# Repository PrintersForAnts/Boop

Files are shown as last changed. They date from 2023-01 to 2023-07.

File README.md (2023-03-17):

# Boop

Add nozzle probing to your [Printer For Ants](https://www.3dprintersforants.com).

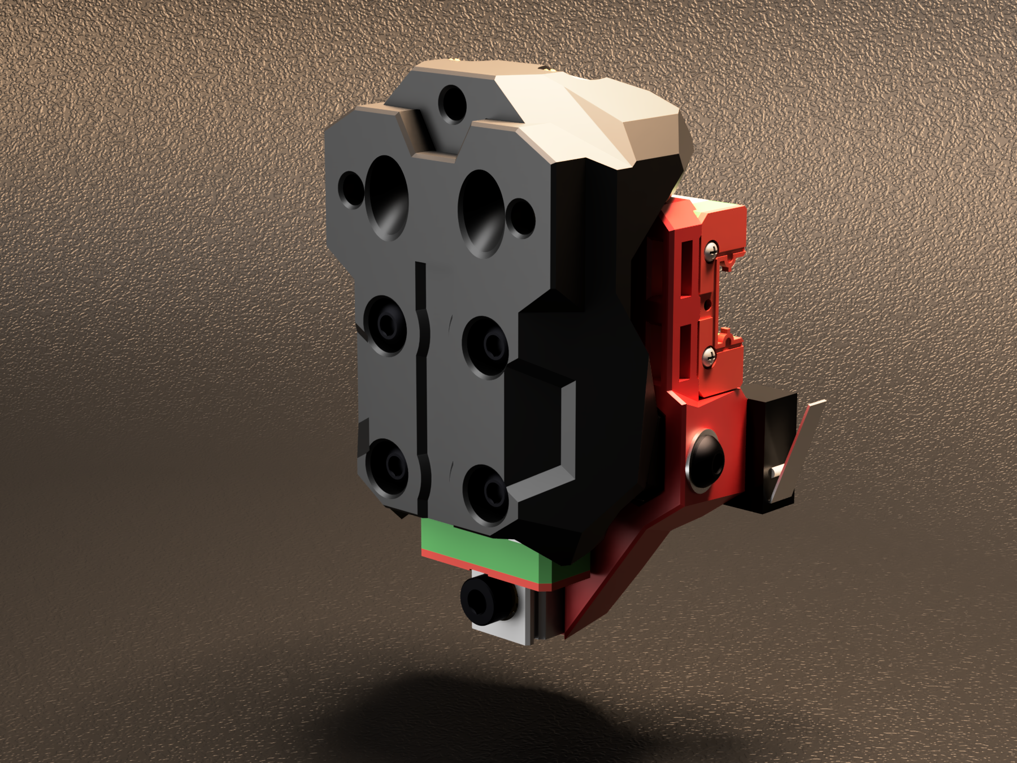
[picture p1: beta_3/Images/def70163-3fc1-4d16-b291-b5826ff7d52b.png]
boop_beta-3_render


Boop is a down-scaled version of the [Voron Tap](https://github.com/VoronDesign/Voron-Tap/) nozzle-based Z probe, and has been carefully optimized for [Printers for Ants](https://3dprintersforants.com) that have front-facing MGN9 rails and rock Voron V0.2-style toolheads.

Just like [Tap](https://github.com/VoronDesign/Voron-Tap/) - with Boop, the entire toolhead moves to trigger an optical switch, which offers many advantages, including:
* **excellent precision**: sub .001mm in some cases - microstep-level!!!
* **excellent reliability**: an effectively infinite number of probing cycles
* **software simplicity**: simplified macro configuration

... and more, as noted on the Tap [README](https://github.com/VoronDesign/Voron-Tap/).  It's great.

## Version History

**2023-03-14: beta-3 release by MasturMynd!** :pie:

A new two-part, centered-sensor design brings major practical improvements:
* **stronger**: more beef + two-part design + built-in strengthening slots
* **easier to print**: reduced/simplified supports + uses standard Voron settings
* **easier to evolve**: two-part design enables faster iteration and the potential for rear V0.2-style heatsets
* **now supports Tap sensor boards!**

**2023-02-08: beta-2 release by Yeri** - resolved some small interferences.  Files on DoomCube Discord, if you need them.

**2023-01-08: beta-1 release by Yeri!** :tada: proof that you can fit the Tap concept onto a much smaller printer, in a much tighter space.

## Requirements

* Bed must be stable for high probing force
    * Not a fit for cantilevered-bed printers, including V0 and Tiny-M
* Front-facing MGN-9H X-axis rail
* V0.2-style toolhead with 2 holes in front, 1 in back
    * Supports MiniSB
* 5/24V required at toolhead

**NOTE**: As of beta-3, other toolheads based on the MiniAB mounting pattern are *not* officially supported, such as the MiniAB, MiniAS, and others.

## Instructions

** CHECK THE STL DIRECTORIES FOR SPECIFIC INSTRUCTIONS! **

Much of the [Voron Tap](https://github.com/VoronDesign/Voron-Tap/blob/main/Manual/Assembly_Manual_Tap.pdf) manual applies here; read through it first.  

In particular, note the section about adjusting the bed forwards.

1. Update your `printer.cfg` as recommended in [Tap Klipper Instructions](https://github.com/VoronDesign/Voron-Tap/blob/main/config/tap_klipper_instructions.md)
2. Home Z and test virtual Z endstop by lifting tool-head
3. Heat soak your machine and run a couple `probe_accuracy samples=100` to "break-in" your probe
4. Run a few more `probe_accuracy` checks (default of 10 probes)

## BOM

** CHECK THE STL DIRECTORIES FOR SPECIFIC BOM **

**An MGN9H rail sized for your specific printer will be needed.**  See below for printer compatibility and sizes.

## Compatibility Chart & Rail Sizes

| Printer | Rail and Notes |
| - | - |
| [Salad Fork](https://github.com/PrintersForAnts/Salad_Fork) 120 | ✅ MGN9H 180 |
| [Salad Fork](https://github.com/PrintersForAnts/Salad_Fork) 160 | ✅ MGN9H 210 |
| [Micron](https://github.com/PrintersForAnts/Micron) 120 | ✅ MGN9H 150 |
| [Micron](https://github.com/PrintersForAnts/Micron) 180 | ✅ MGN9H 220 |
| [Pandora Gantry](https://github.com/MasturMynd/Pandora) 120 | ✅ MGN9H 200 |
| [Pandora’s Box](https://github.com/MasturMynd/Pandoras_Box) 120 | ✅ MGN9H 200 |
| [Tiny-T](https://github.com/PrintersForAnts/Tiny-T) 150  | ✅ MGN9H 200 |
| [Tri-Zero](https://github.com/zruncho3d/tri-zero) 120 | ❓ MGN9H 200 (!!!) Requires either [Pandora Gantry](https://github.com/MasturMynd/Pandora) or the gantry from [Pandora’s Box](https://github.com/MasturMynd/Pandoras_Box) along with a gantry brace from the mods folder. <p><p> Note: The Boop carriage can hit the Z extrusions of the stock frame. For this reason, print volume will be reduced. | [F-Zero](https://github.com/zruncho3d/f-zero) | ❓ MGN9H 200 (!!!) Requires the [Pandora Gantry](https://github.com/MasturMynd/Pandora) |
| [Voron Zero](https://github.com/VoronDesign/Voron-0), [Tiny-M](https://github.com/gsl12/Tiny-M) | ❌ Cantilevered beds are not a fit.  |
| [Dueling Zero](https://github.com/zruncho3d/DuelingZero) | ❌ Not supported, as a front-facing gantry is required, and clearance to the vertically-oriented Z extrusions would be needed |

## FAQ

All [Voron Tap FAQs](https://github.com/VoronDesign/Voron-Tap/#faqs) apply here too!

If you don’t see an answer for your question, the place to ask is the `#boop` channel in the [DoomCube Discord](https://discord.gg/doomcube).

### Does this move my toolhead around?
Yes, a bit, and your bed mount will require a corresponding adjustment forwards.

### Is there a top-mount Boop version for my Tri-Zero?
Not at this time.  Seems hard to design, because the right angle of a V0 mount would create the potential for flex.   Perhaps with metal reinforcements, this could work, but you would run into the door and lose space.

### Where’s the manual?
So much of the design is shared with Voron Tap that a README here will have to suffice for now.

### Is there a circuit board?
Yes! Beta-3 adds support for the OptoTap board, intended for Tap!

### Is there a version for V0?
No.  Cantilevered beds are not a fit for Tap/Boop-style probing, where significant force is involved.

### Is there a version for MGN9C rails?
Yeri tried to make it work with a 9C rail, but Fusion 360 doesn’t support wormhole technology and the screws interfered with the 50mm rail.  

### Can I just move a 9H carriage over?
Unlikely, unless these are from the same batch and manufacturer.

### Do I need new belts to use Boop?
No; existing ones should be fine as long as you didn't trim the belts too close to the existing carriage

### Could I put this on an MGN9-front-rail printer like MGN9 V2?
Yes.  It would be smaller and lighter than Tap, and enable the use of the V0-style toolhead ecosystem.  ???

## Credits

`clee` tested the beta parts and provided feedback.

`DoubleT` tested the beta parts and provided feedback.

`hartk` did initial beta testing and feedback.

`Kyleisah` provided the beautiful render of Boop beta-3.

`L.e.o.p.a.r.d.` tested beta-3, provided feedback and is working on alternative methods of triggering boop.

`Mastur_Mynd` developed beta-3, taking many design queues from both beta-2 as well as Voron Tap.

`pnewb` tested beta-3 and provided feedback and criticism.

`Steve` tested beta-3, provided feedback and previewed live on stream!

`Yeri` did the original and following CAD work and is the project lead.

`Zruncho` did testing, some CAD exploration, and wrote the initial README.

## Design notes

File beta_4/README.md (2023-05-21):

## Beta-4 Features

* Redesigned to use parts from Voron Tap RC8 with the exception of M3x40 BHCS instead of M3x50 SHCS
* Belting redesigned to use clamps rather than only trapping belts between the carriage and printed part
* Steeper magnet angle to reduce trigger force and toolhead wobble
* Option to use 4x magnets for greater force
* Rear heatset inserts are further away from the linear rail to prevent loosening as quickly over time
* Less support material
* Improved supports for [a]_boop_center_optical to allow more robust parts

## Instructions

Print 7 parts:
1. [a]_boop_center_optical.stl
2. [a]_belt_clamp_x2.stl
3. [a]_belt_clamp_x2.stl
4. boop_front.stl
5. boop_upper_optical.stl _or_ boop_upper_pcb.stl
6. magnet_carrier_left.stl
7. magnet_carrier_right.stl

For each, Voron-standard settings are recommended. The front and center pieces have internal features to improve rigidity, similar to how Tap does.

## BOM

The core Boop requires a sensor, short rail, magnets, and various fasteners. Boop beta-3 also adds support for OptoTap boards.

| Type | Part | Qty | Link | Note |
| - | - | - | - | - |
| Electronics | OPB991P51Z<p><p>2nd choice: OPB990P51Z | 1 | [Digi-Key: OPB991P51Z](https://www.digikey.com/en/products/detail/tt-electronics-optek-technology/OPB991P51Z/1637791)<p><p>2nd choice: [Digi-Key: OPB990P51Z](https://www.digikey.com/en/products/detail/tt-electronics-optek-technology/OPB990P51Z/1637770) | The 991 sensor is strongly recommended as it is safe for MCUs that cannot tolerate 5v input signals. If you have a MCU that is 5v safe then the 990 can be used. Please verify your MCUs capabilities before ordering! |
| | 220 ohm, 1/4 watt | 1 | | |
| Rail | MGN9H 50mm | 1 | | |
| Fasteners | M2x10 Self Tapping Screw | 1 | | |
| | M3x6 BHCS | 10 | | |
| | M3x8 BHCS | 3 | | |
| | M3x10 BHCS | 2 | | |
| | M3x40 BHCS | 2 | | |
| | M3x6 SHCS | 1 | | |
| | M3x12 SHCS | 1 | | |
| | M3x16 SHCS | 3 | | |
| | M3x6 FHCS | 2 | | black oxide or other magnetic alloy required |
| | M3 Hex Nut | 3 | | |
| | M3 Washer | 2 | | |
| | M3 Threaded Insert v3 | 9 | | |
| | 6x3mm Magnet | 4 | | |

## Technical Data
*Coming Soon*

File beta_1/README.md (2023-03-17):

## Instructions

Print 4 parts:
1. Boop_Center.stl
2. front part (X_Carriage_Front_Mini_Afterburner.stl or X_Carriage_Front_Mini_Stealthburner.stl).  

For both, Voron-standard settings will work, however higher infill and perimeters are recommended, as you want this part to be strong.

## BOM

The core Boop requires a sensor, short rail, magnets, and various fasteners.

| Type | Part | Qty | Link | Note |
| - | - | - | - | - |
| Sensor | OPB991P51Z<p><p>2nd choice: OPB990P51Z | 1 | [Digi-Key: OPB991P51Z](https://www.digikey.com/en/products/detail/tt-electronics-optek-technology/OPB991P51Z/1637791)<p><p>2nd choice: [Digi-Key: OPB990P51Z](https://www.digikey.com/en/products/detail/tt-electronics-optek-technology/OPB990P51Z/1637770) | The 991 sensor is strongly recommended as it is safe for MCUs that cannot tolerate 5v input signals. If you have a MCU that is 5v safe then the 990 can be used. Please verify your MCUs capabilities before ordering! |
| Magnet | 6mm n52 magnets | 2 | | |
| Rail | MGN9H 50mm | 1 | | |
| Electronics | 220 ohm, 1/4 watt | 1 | | |
| Fastener | M3 hex nut | 1 | | |
| Fastener | M3 heatset inserts | 4 | |
| Fastener | M3x6 BHCS | 3 | | |
| Fastener | M3x6 FHCS | 2 | | black oxide or other magnetic alloy required |

## Probe Accuracy Samples

Microstep-level precision is possible with Boop!  Sample outputs, from the PROBE_ACCURACY command built into Klipper:

#### Yeri’s Salad Fork

```
probe accuracy results: maximum -0.507500, minimum -0.508750, range 0.001250, average -0.508650, median -0.508750, standard deviation 0.000339
```

#### Hartk’s Micron

```
probe accuracy results: maximum 0.016852, minimum 0.16227, range 0.000625, average 0.016477, median 0.016540, standard deviation 0.000187
```

#### Zruncho’s PB0-over-T0 Testbed

```
probe accuracy results: maximum -1.504824, minimum -1.509824, range 0.005000, average -1.507536, median -1.507324, standard deviation 0.001016
```

This is a [custom testbed with a Pandora’s Box gantry atop a Tri-Zero lower](https://photos.app.goo.gl/bsP73i9GyqMNQoTf8).  Unlike the two above, this setup is direct-drive, with no reduction.

This number was made possible by increasing the microstepping to 128x to yield a 0.00125 microstep size.

#### DoubleT’s TinyT

```
probe accuracy results: maximum 0.010000, minimum 0.003750, range 0.006250, average 0.005775, median 0.005000, standard deviation 0.001730
```

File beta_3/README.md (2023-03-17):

## Beta-3 Features

* balances the sensor by placing it in the center
* adds rigidity, from more material as well as built-in strengthening slots
* two-part front design reduces the area with supports, plus makes the design easier and faster to evolve
* supports Tap sensor boards
* easier to print:  you don't know need to worry about the bridge angle settings anymore
* enables the addition of V0.2-style rear heatsets
* bowden toolheads specific for beta-3 (the default bowden mini stealthburner toolhead has a lip that prevents it from seating properly).

## Instructions

Print 5 parts:
1. [a]_boop_center_optical.stl
2. boop_front.stl
3. boop_upper_optical.stl _or_ boop_upper_pcb.stl
4. magnet_carrier_left.stl
5. magnet_carrier_right.stl

For each, Voron-standard settings are recommended. The front and center pieces have internal features to improve rigidity, similar to how Tap does.

## BOM

The core Boop requires a sensor, short rail, magnets, and various fasteners. Boop beta-3 also adds support for OptoTap boards.

| Type | Part | Qty | Link | Note |
| - | - | - | - | - |
| Electronics | OPB991P51Z<p><p>2nd choice: OPB990P51Z | 1 | [Digi-Key: OPB991P51Z](https://www.digikey.com/en/products/detail/tt-electronics-optek-technology/OPB991P51Z/1637791)<p><p>2nd choice: [Digi-Key: OPB990P51Z](https://www.digikey.com/en/products/detail/tt-electronics-optek-technology/OPB990P51Z/1637770) | The 991 sensor is strongly recommended as it is safe for MCUs that cannot tolerate 5v input signals. If you have a MCU that is 5v safe then the 990 can be used. Please verify your MCUs capabilities before ordering! |
| | 220 ohm, 1/4 watt | 1 | | |
| Rail | MGN9H 50mm | 1 | | |
| Fasteners | M2x10 Self Tapping Screw | 1 | | |
| | M3x6 BHCS | 8 | | |
| | M3x8 BHCS | 2 | | |
| | M3x10 BHCS | 4 | | |
| | M3x6 FHCS | 2 | | black oxide or other magnetic alloy required |
| | M3x6 SHCS | 1 | | |
| | M3x8 SHCS | 1 | | |
| | M3x12 SHCS | 1 | | |
| | M3 Heatset Inserts | 9 | |
| | M3 Hex Nut | 1 | | |
| | M3 Washer | 2 | | |
| | 6mm n52 magnets | 2 | | |

## Technical Data
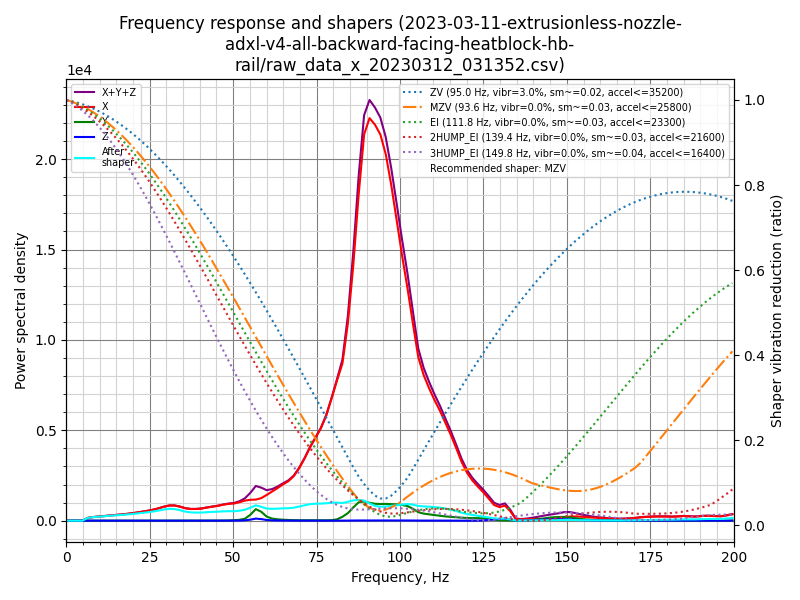
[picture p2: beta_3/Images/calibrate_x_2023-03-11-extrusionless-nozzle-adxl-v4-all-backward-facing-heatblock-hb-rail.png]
x_input_shaper_graph

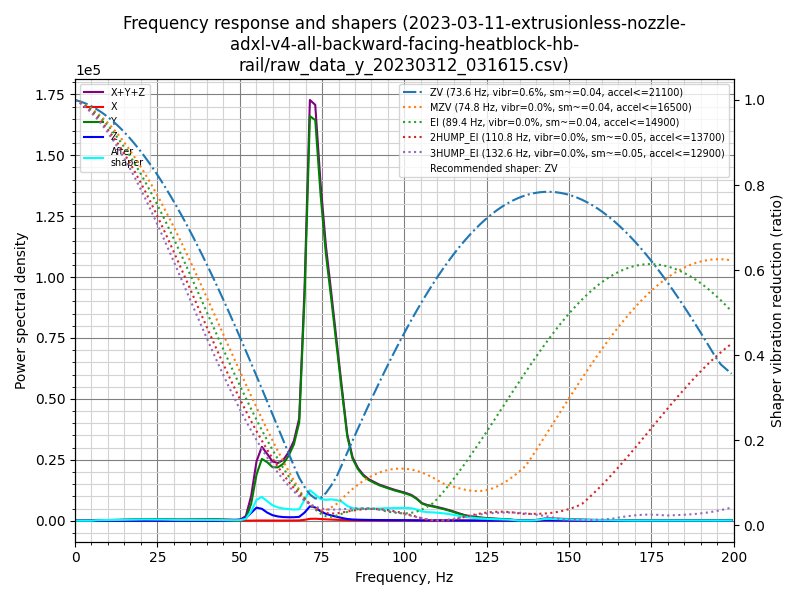
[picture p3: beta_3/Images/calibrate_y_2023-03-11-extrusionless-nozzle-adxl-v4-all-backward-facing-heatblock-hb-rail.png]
y_input_shaper_graph

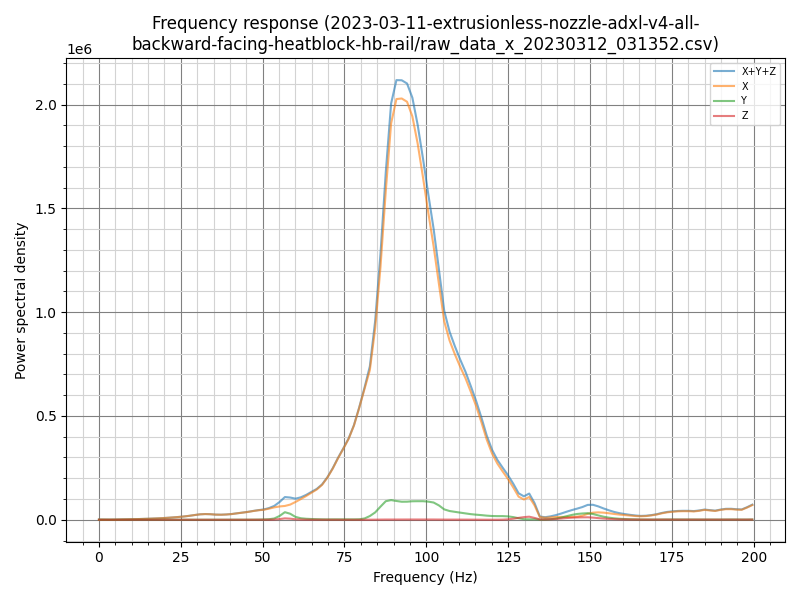
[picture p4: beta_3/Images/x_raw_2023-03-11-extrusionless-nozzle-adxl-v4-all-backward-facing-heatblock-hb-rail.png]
x_raw_data

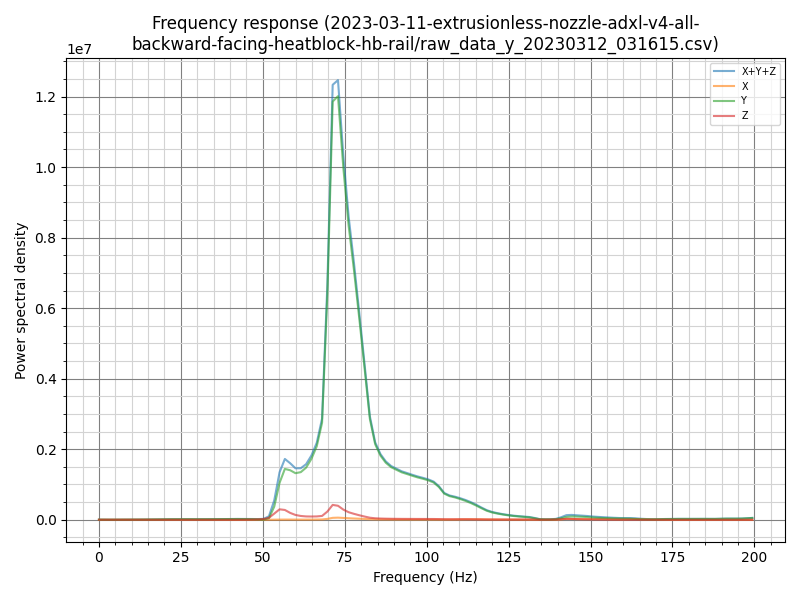
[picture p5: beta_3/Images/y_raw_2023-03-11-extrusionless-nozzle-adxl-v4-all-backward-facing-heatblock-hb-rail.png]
y_raw_data


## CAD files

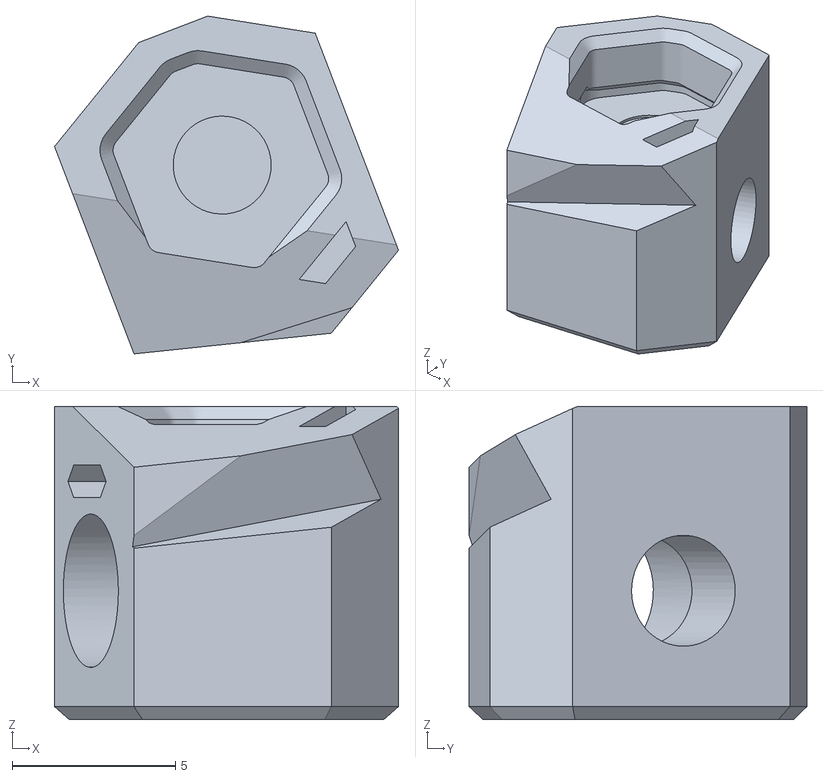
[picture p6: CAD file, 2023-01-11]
beta_1/STL/Tap_Magnet_Right_r1.stl
10.5 x 10.3 x 9.60

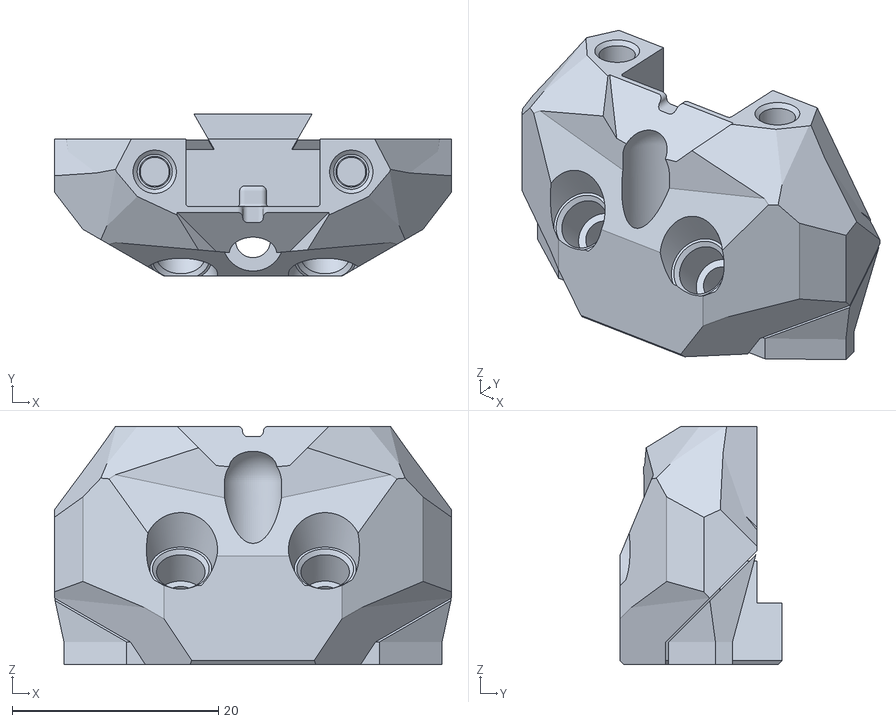
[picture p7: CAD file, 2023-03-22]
beta_3/STL/boop_upper_pcb.stl
38.5 x 15.8 x 23.1

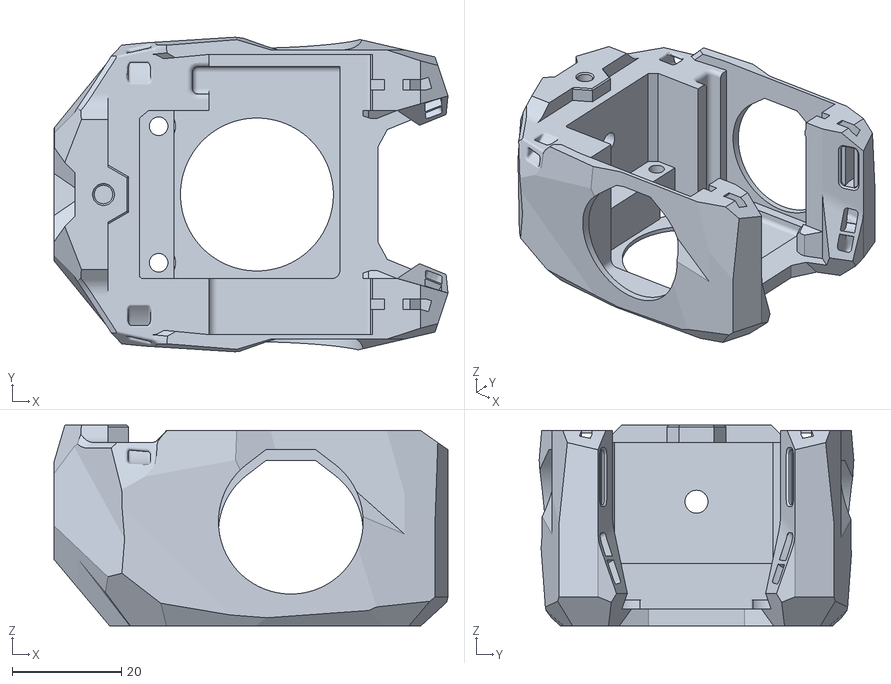
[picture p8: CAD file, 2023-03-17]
beta_3/STL/bowden_toolheads/bowden_cowling_pc4_m10.stl
72.2 x 57.6 x 36.7

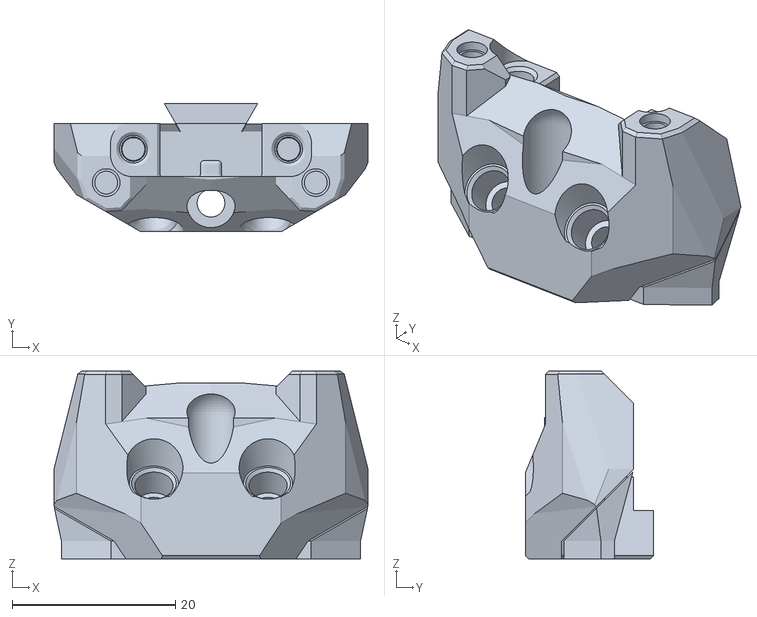
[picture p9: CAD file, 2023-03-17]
beta_3/STL/mods/zruncho/boop_upper_2x_heatsets_plus_supports.stl
38.5 x 15.8 x 23.1

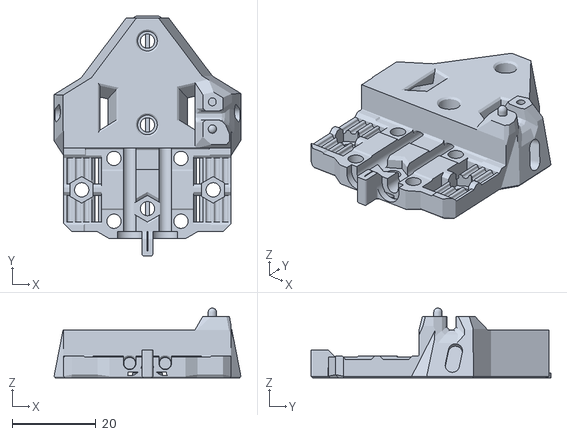
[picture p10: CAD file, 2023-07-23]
beta_4/STL/[a]_boop_center_optical_3mm_belt_spacing.stl
44.6 x 57.3 x 16.7

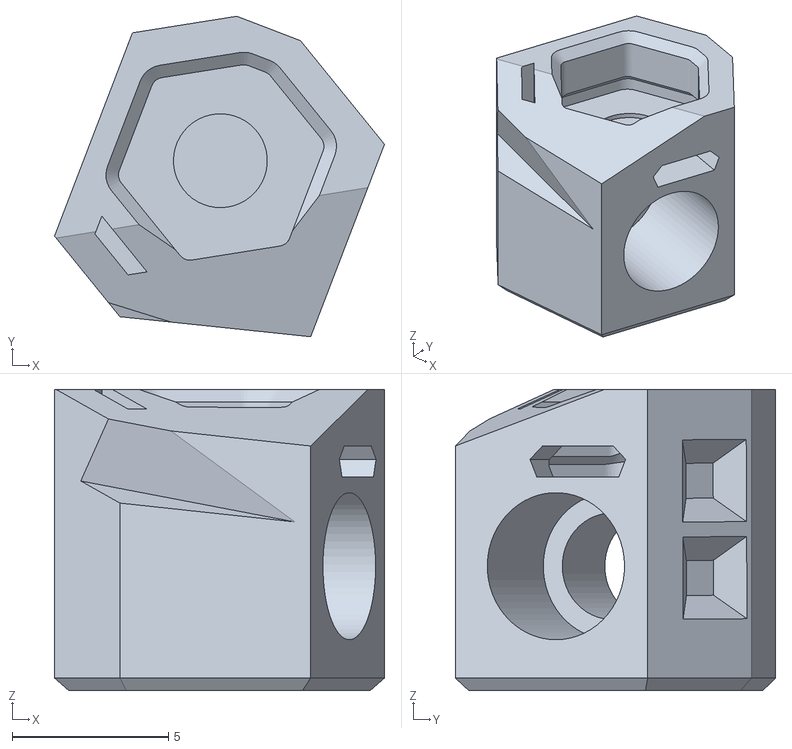
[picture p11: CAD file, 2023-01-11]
beta_1/STL/Tap_Magnet_Left_r1.stl
10.5 x 10.2 x 9.63

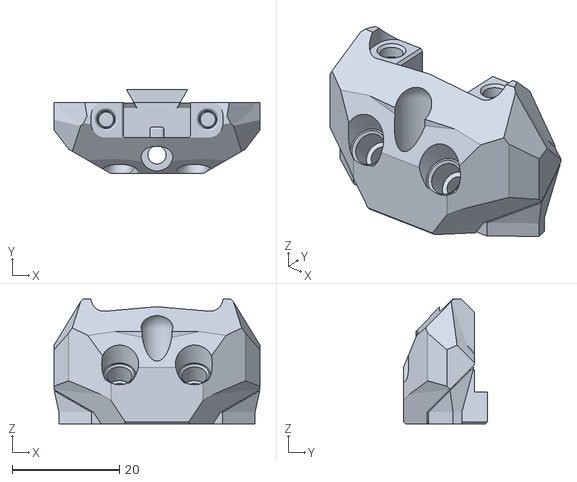
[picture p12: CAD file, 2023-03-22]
beta_3/STL/boop_upper_optical.stl
38.5 x 15.8 x 23.3

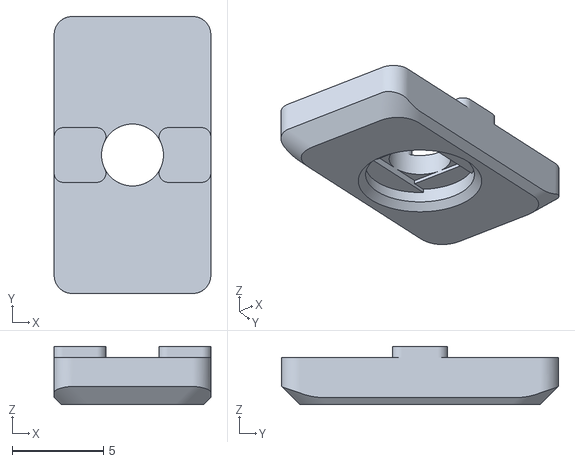
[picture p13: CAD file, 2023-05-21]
beta_4/STL/[a]_belt_clamp_x2.stl
8.60 x 15.2 x 3.20

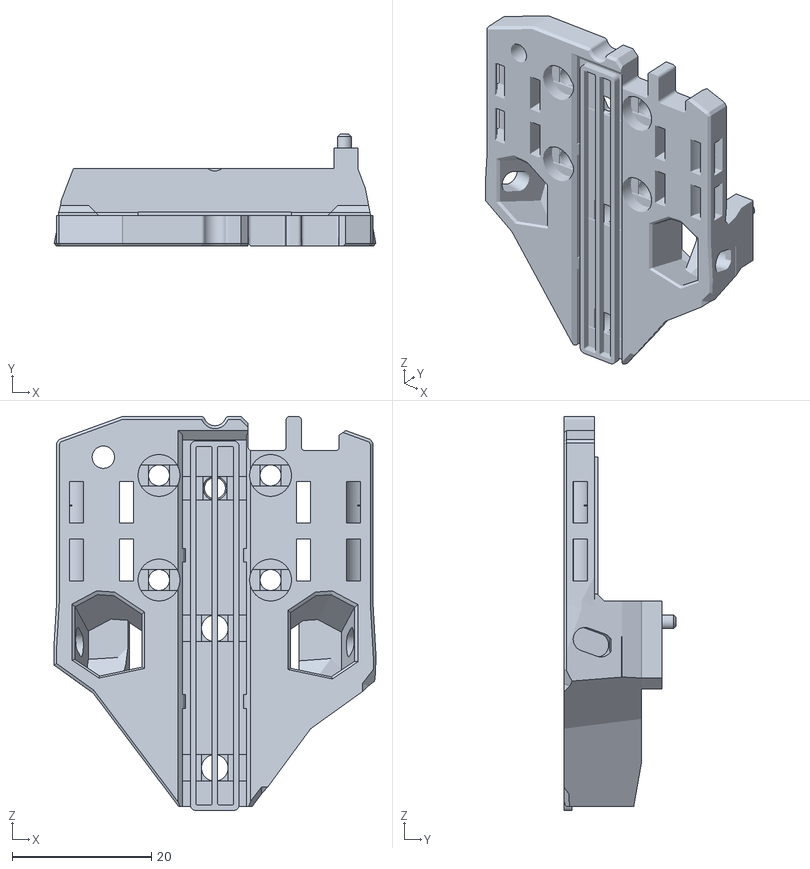
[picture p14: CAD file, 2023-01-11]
beta_1/STL/Boop_Center.stl
46.1 x 16.1 x 56.5

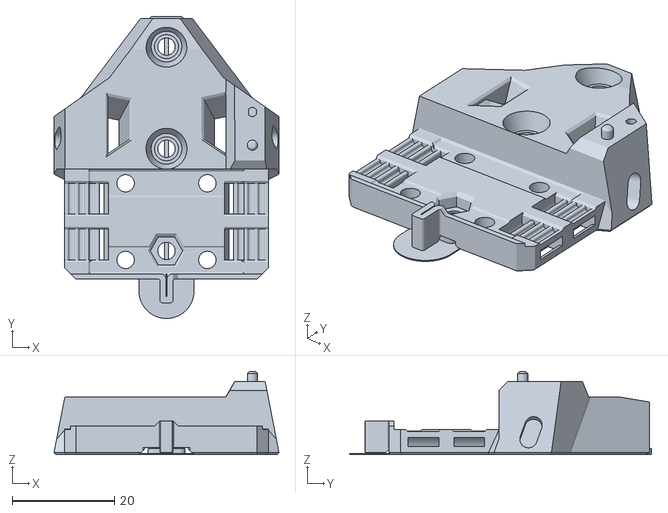
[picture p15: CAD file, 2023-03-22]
beta_3/STL/[a]_boop_center_optical.stl
44.0 x 59.1 x 16.3

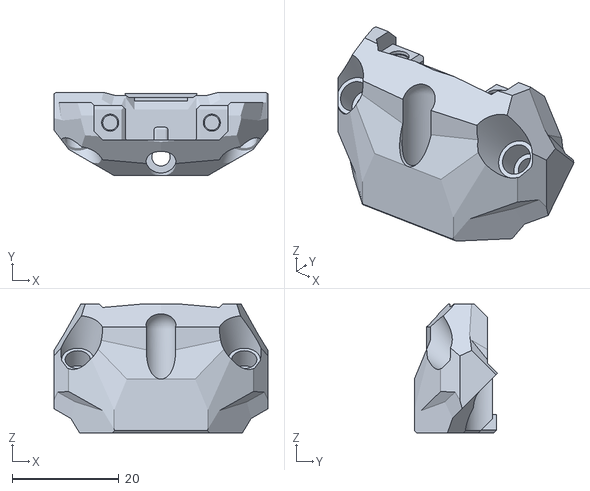
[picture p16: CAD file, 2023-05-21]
beta_4/STL/boop_upper_wired.stl
40.0 x 15.6 x 24.0

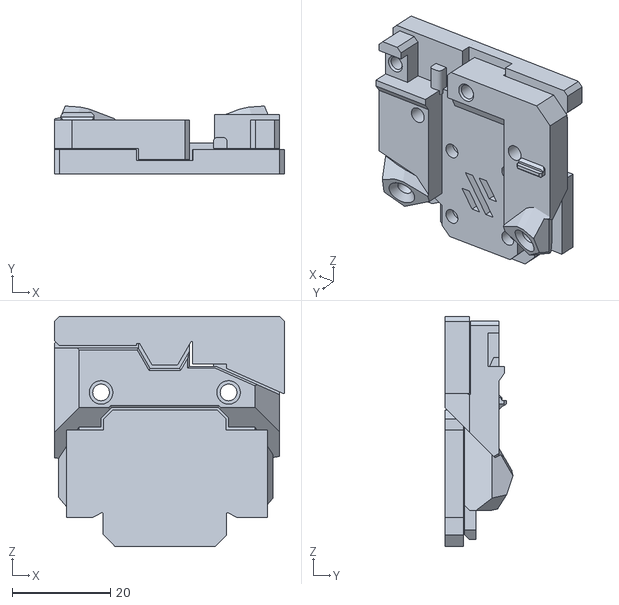
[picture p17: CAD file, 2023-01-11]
beta_1/STL/X_Carriage_Front_Mini_Stealthburner.stl
46.9 x 13.9 x 46.9

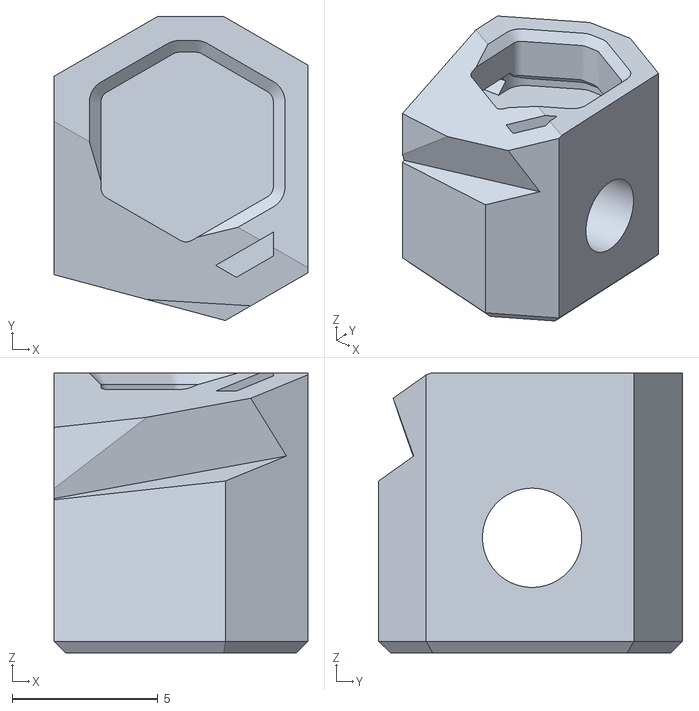
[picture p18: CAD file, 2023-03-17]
beta_3/STL/magnet_carrier_right.stl
8.70 x 10.4 x 9.60

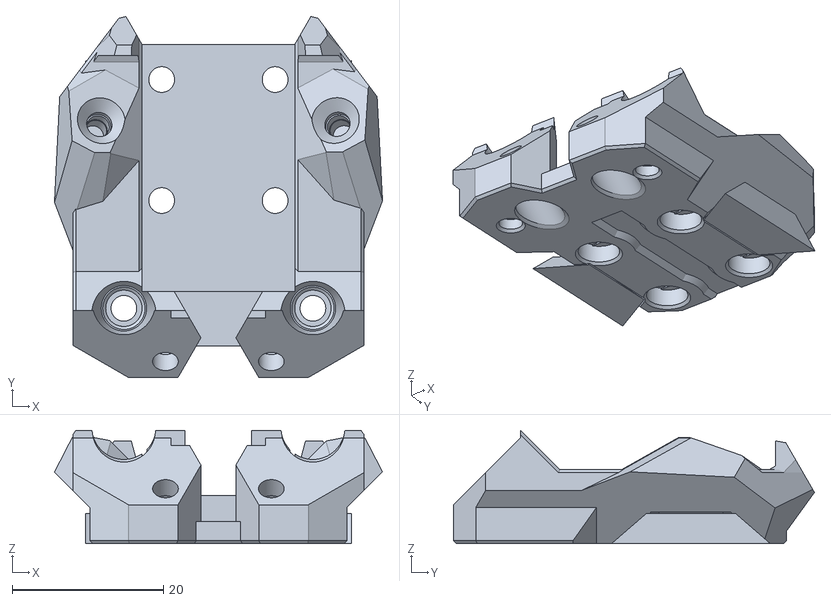
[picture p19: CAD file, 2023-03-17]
beta_3/STL/boop_front.stl
43.4 x 47.7 x 15.0

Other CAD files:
beta_3/STL/bowden_toolheads/bowden_cowling_ecas04.stl
beta_4/STL/[a]_boop_center_optical_4mm_belt_spacing.stl
beta_1/STL/X_Carriage_Front_Mini_Afterburner.stl
beta_4/STL/boop_front.stl
beta_3/STL/magnet_carrier_left.stl
beta_4/STL/boop_upper_pcb.stl

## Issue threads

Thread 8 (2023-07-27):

Boob4 is to long so nozzel is not touching the bed

Toogo, 2023-07-27:
Printed the Boop4, using Pheatus Voron Dragon Hotend, MiniAB toolhead. The nozzel is lower than the Boop.
Solution is to lower the toolhead mounting holes.

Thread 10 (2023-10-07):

Micron 120, MGN 9G 150 rail note

Flipsoul, 2023-10-07:
Add note to Compatibility Chart & Rail Sizes table for Micron 120 to identify a loss of 10mm in X travel due to longer carriage size

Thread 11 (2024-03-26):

Manual for Beta 4 is sorely needed

ccfman2004, 2024-03-26:
I've been trying to put together Boop Beta 4 but trying to follow the Tap manual doesn't help since there are enough differences between Boop Beta 4 and current version of Tap I am not sure how to assemble Boop.

For exampleL for the 50mm rail the tap manual has the middle bolt as M3x8 and the bottom bolt as M3x12. With Boop Beta 4 those are too short (unless I am doing something wrong as I have the heat inserts as far in as I can get them to go). I had to use an M3x12 for the middle bolt and M3x16 for the bottom. Correct if this is incorrect.

Also I have no idea where the remaining 7 heat inserts go.

I cannot use Fusion 360 to load the CAD file as it doesn't have a dark mode (as far as I can tell) and I cannot read the interface at all in light mode until I have eye surgery.

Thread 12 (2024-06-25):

Boop does not fit Dragon Burner

maximiliandrey, 2024-06-25:
Hi, the front of Boop does not fit the Dragon Burner. Is there a possibility to get this customized for it? I am currently building a Micron+ and would like to use Boop in combination with the Dragon Burner?

Thank you very much and kind regards,

maximiliandrey, 2024-06-25:
Never mind, problem solved. Found solution on https://github.com/chirpy2605/voron/tree/main/general/Alternative_Voron_Mounts/Modified_Mounts

Kind regards.

Closed 2024-06-25.

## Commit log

2023-01-11 Added beta 1 stl files
    [Boop_Center.stl, X_Carriage_Front_Mini_Afterburner.stl, X_Carriage_Front_Mini_Stealthburner.stl]
2023-01-11 Added Tap R1 magnet holders
    [Tap_Magnet_Left_r1.stl, Tap_Magnet_Right_r1.stl]
2023-03-17 Beta-3 Release
    Introduced beta-3 to the repo and reorganized.
    [Boop_Center.stl, Tap_Magnet_Left_r1.stl, Tap_Magnet_Right_r1.stl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]
2023-03-19 Adjusted PCB mounting
    Moved mounting for boop_upper_pcb back 1.8mm to prevent triggering issues.
    [boop_upper_pcb.stl]
2023-03-21 Corrected Probe Positioning
    The probe flag wasn't thick enough to reliably trigger the optical switch. Adjusted mounting for each 1.8mm towards the back and extended the front of the flag to improve trigger reliability.
    [[a]_boop_center_optical.stl, boop_upper_optical.stl, boop_upper_pcb.stl]
2023-03-22 Uploaded CAD
    I forgot the CAD in my previous update
2023-05-20 beta4 initial release
    [[a]_belt_clamp_x2.stl, [a]_boop_center_optical.stl, boop_front.stl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]
2023-07-23 Added 3mm belt spacing
    The initial commit only had a 4mm belt spacing option. This is intended for 2020 based printers where 1mm shims are used for bearing stacks.
    [[a]_boop_center_optical_3mm_belt_spacing.stl, [a]_boop_center_optical_4mm_belt_spacing.stl]
